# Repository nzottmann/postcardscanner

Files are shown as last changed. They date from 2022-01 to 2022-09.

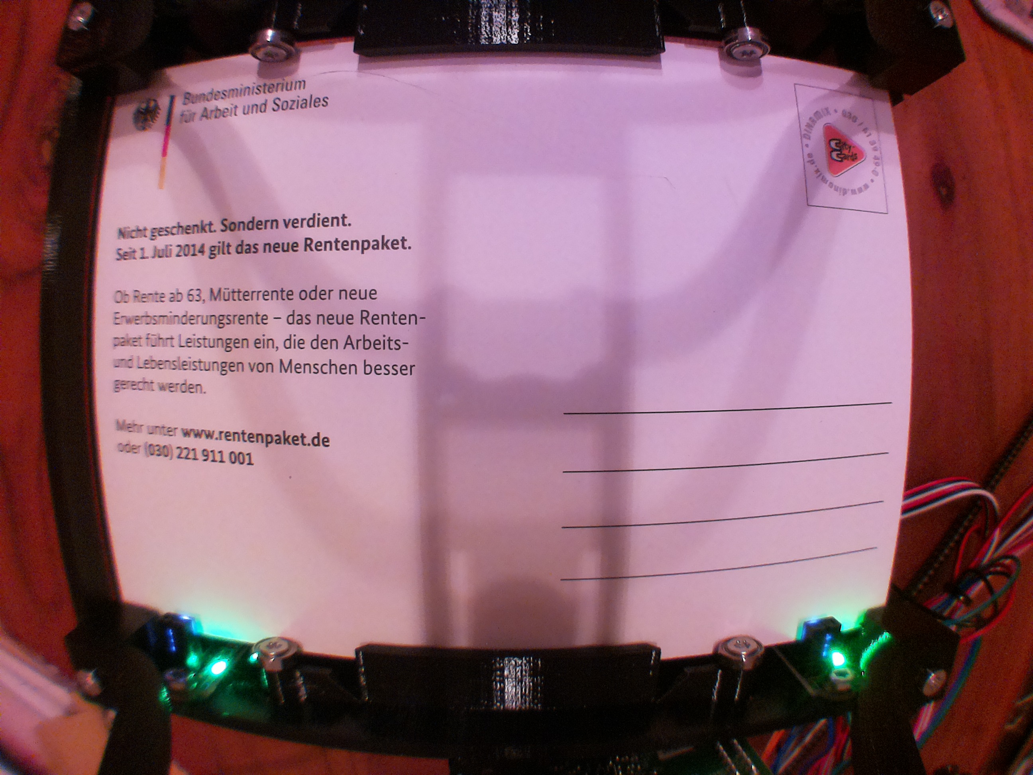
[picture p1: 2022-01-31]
examples/example.jpg

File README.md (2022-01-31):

Python library for postcard scanner

# Installation
Installation manual is for linux, tested on Raspberry Pi (Raspberry Pi OS, bullseye, Release date: January 28th 2022)
- Install Python >=3.5.
- Install python venv
    ```
    sudo apt-get install python3-venv
    ```
- Create and activate virtual environment
    ```
    source venv/bin/activate
    python3 -m venv venv
    ```
- Clone this repo
    ```
    git clone https://github.com/nzottmann/postcardscanner.git
    ```
- Install `postcardscanner`
    ```
    pip install -e postcardscanner
    ```
- Run example
    ```
    cd postcardscanner/examples
    python scanner_demo.py
    ```
    Output:
    ```
    DEBUG:postcardscanner:state: enabled
    Received image
    DEBUG:postcardscanner:state: scanning
    DEBUG:postcardscanner:state: enabled
    ```
    `img.jpg` is now a copy of `example.jpg`

# Usage
Examples in `examples` folder show how to use this library.

## Examples

### scanner_v0.py
Example for using the first hardware prototype, v0

### scanner_demo_camera.py
Example for testing without scanner hardware, but with pi camera. Captures images from camera.

### scanner_demo.py
Example for testing without hardware. Input own image for testing or use `example.jpg`.

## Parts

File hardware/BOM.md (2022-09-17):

# Postcardscanner Bill of Materials

## 3D printed Parts

For printing, Prusament PETG and a Prusa printer with a 0.6mm nozzle is recommended. Use supports where necessary.

See 3d construction file for placment of these parts:

- base
- frame-bot (needs supports)
- frame-bot-cover
- frame-top
- 4x sensor cover
- feeder
- belt-cover
- camera
  - camera-mount
  - wall-front
  - wall-back
- 4x roller (use TPU, FilaFlexible40 recommended)

## Mechanical

- Misumi
  - 8x bearings 695DD1 13x5x4mm RS/2RS
  - 1x axis PSFMRR5-140-B2-S18.4
  - 1x axis PSFMRR5-156.4-B18.4-S18.4
  - 4x retainer NETWS4
  - 1x belt GBN2502GT-60 2GT 6mm 250mm
- Amazon
  - 4x Pulley GT2 20 teeth for 5mm shaft, 6mm belt
  - Ruthex M3 brass inserts
- stepperonline
  - Nema 11 Bipolar 1.8deg 7Ncm 28x28x31mm

## Electrical

- Raspberry Pi Camera v2
- Camera flex cable 50cm
- 4x optical endstop
- 12V LED stripe, ~20cm
- Cable

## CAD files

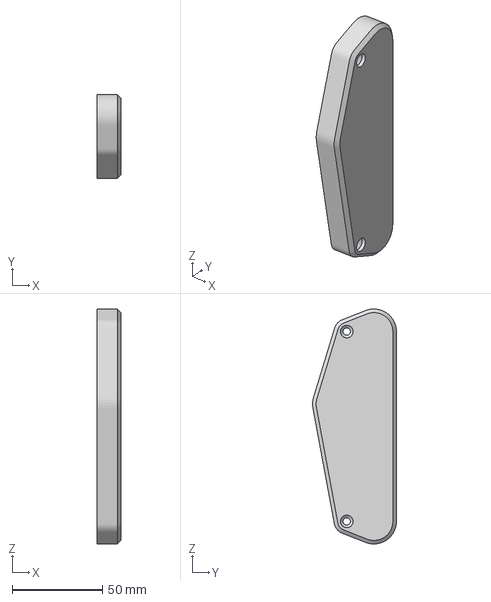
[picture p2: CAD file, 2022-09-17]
hardware/3d printing/belt-cover.3mf
13.2 x 46.4 x 130.0 mm

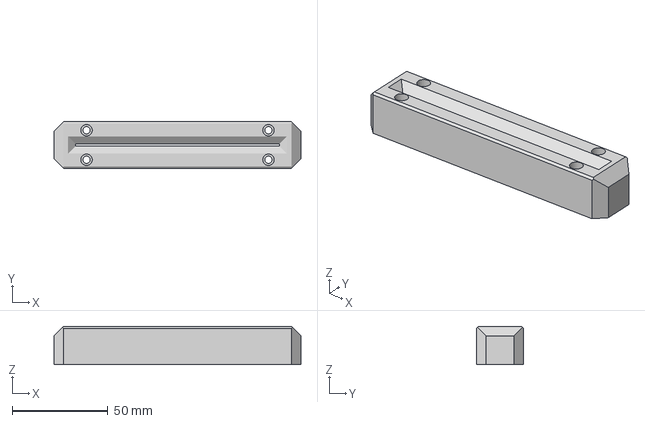
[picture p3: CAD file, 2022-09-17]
hardware/3d printing/feeder.3mf
129.0 x 24.4 x 20.0 mm

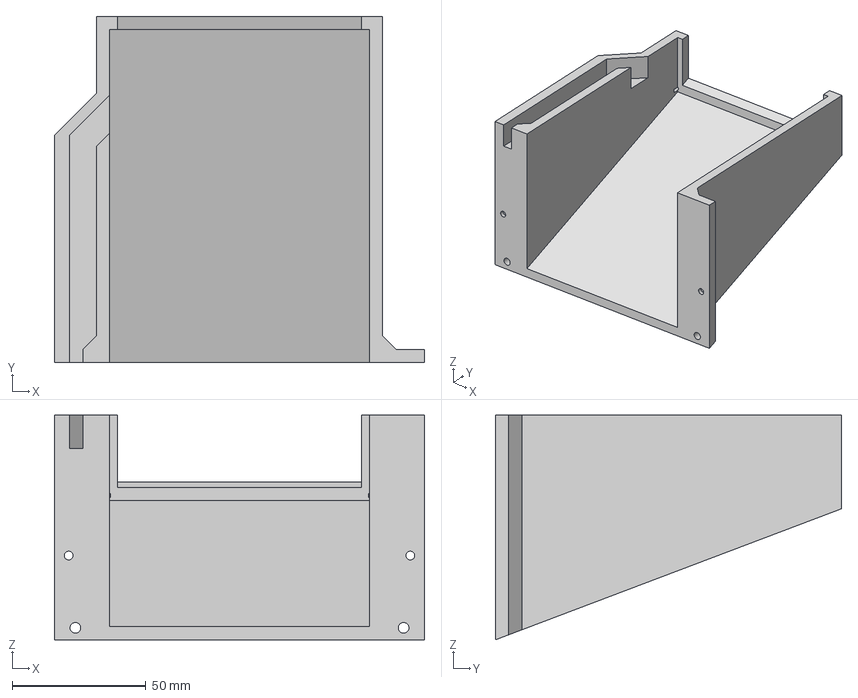
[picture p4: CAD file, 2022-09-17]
hardware/3d printing/wall-back.3mf
138.2 x 129.4 x 84.0 mm

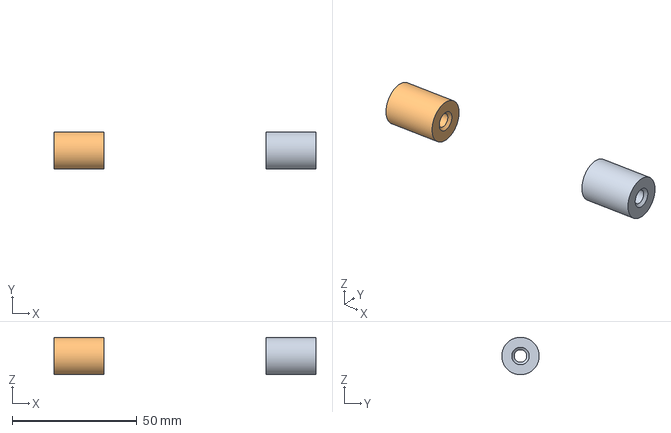
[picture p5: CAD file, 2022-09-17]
hardware/3d printing/roller.3mf
105.0 x 15.0 x 15.0 mm
Körper1
Körper3

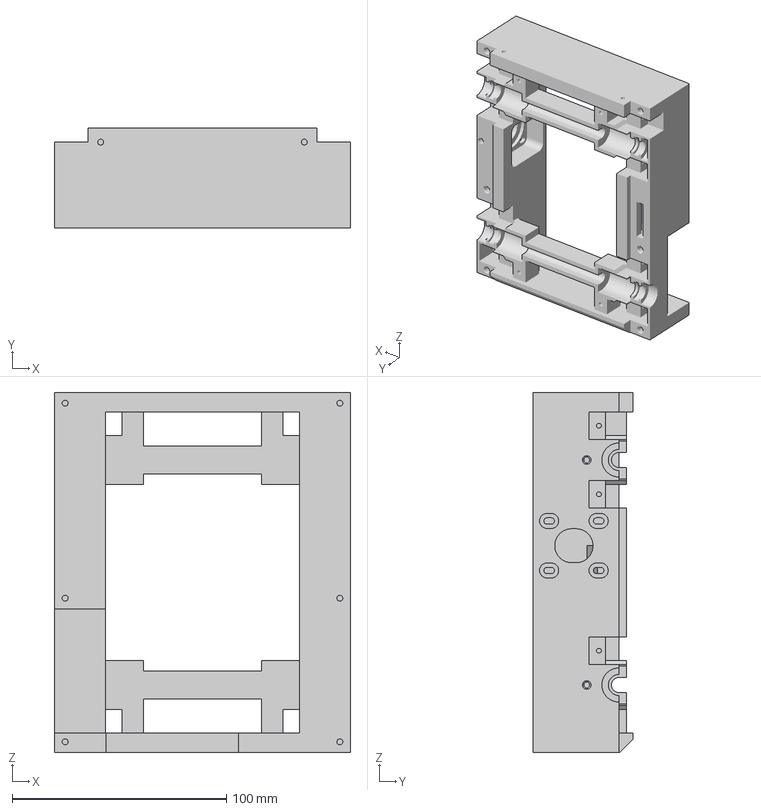
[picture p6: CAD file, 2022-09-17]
hardware/3d printing/frame-bot.3mf
138.2 x 46.5 x 168.0 mm

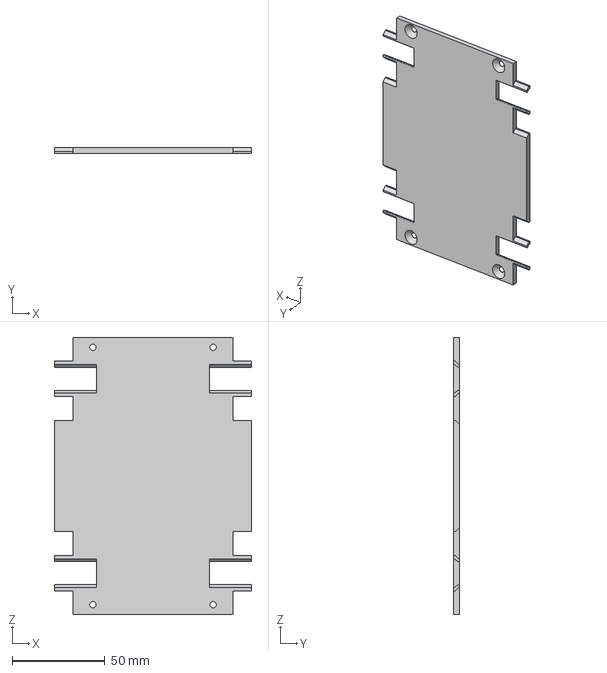
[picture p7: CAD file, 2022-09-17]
hardware/3d printing/frame-bot-cover.3mf
106.6 x 3.00 x 149.6 mm

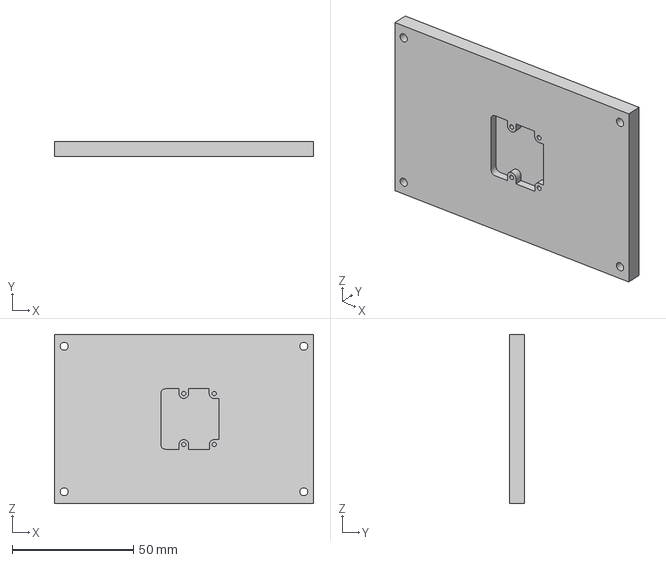
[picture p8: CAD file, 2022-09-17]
hardware/3d printing/camera-mount.3mf
107.0 x 6.00 x 70.0 mm

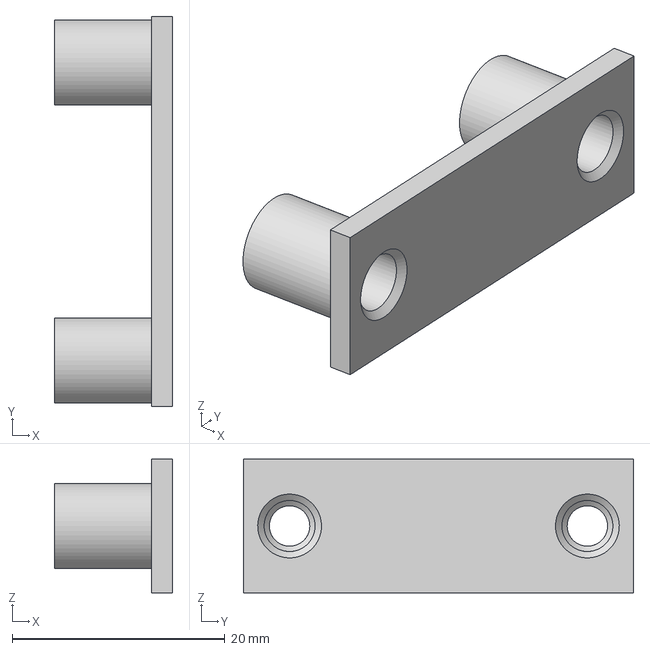
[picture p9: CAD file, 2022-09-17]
hardware/3d printing/sensor-cover.3mf
11.1 x 36.7 x 12.6 mm

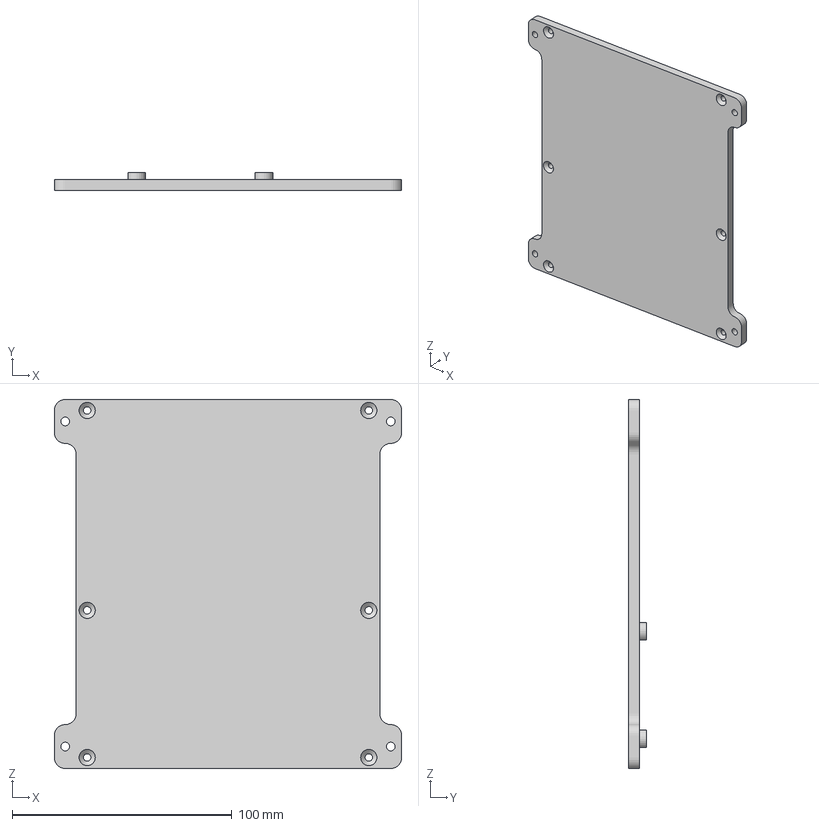
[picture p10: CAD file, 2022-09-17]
hardware/3d printing/base.3mf
158.2 x 8.01 x 168.0 mm

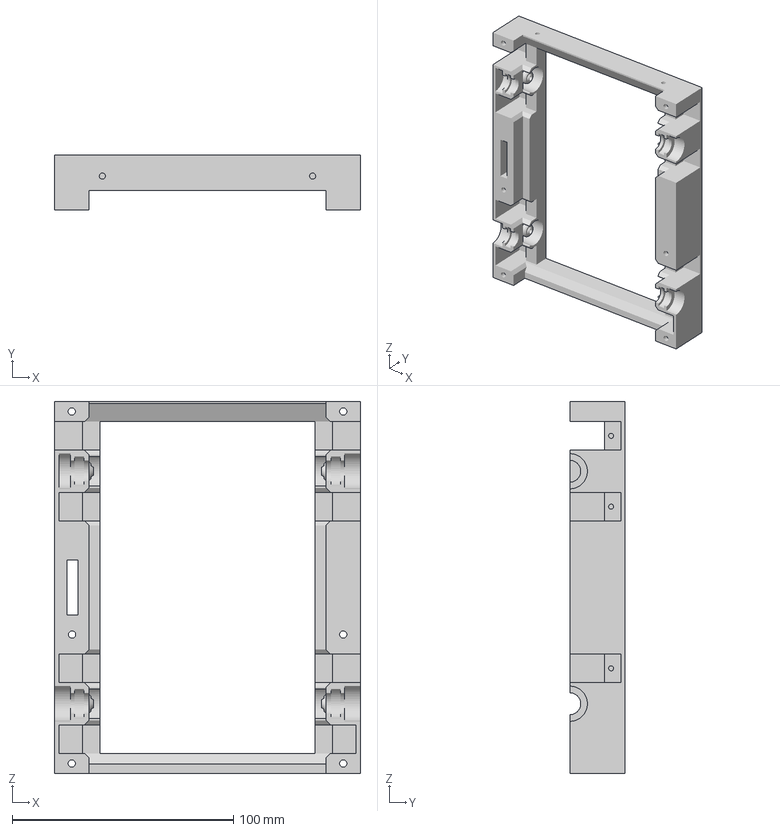
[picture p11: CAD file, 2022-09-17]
hardware/3d printing/frame-top.3mf
138.2 x 25.0 x 168.0 mm

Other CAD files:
hardware/3d printing/wall-front.3mf

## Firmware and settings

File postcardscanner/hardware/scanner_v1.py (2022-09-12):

import logging
logger = logging.getLogger('scanner_v1')
import time
from io import BytesIO
import subprocess
import RPi.GPIO as GPIO
from RpiMotorLib import RpiMotorLib
from .scanner import Scanner
from postcardscanner.states import PostcardScannerState

class ScannerV1(Scanner):
    clockwise = False
    steptype_1 = "Half"
    steptype_2 = "Half"
    stepdelay = .0003
    counter = 0
    def __init__(self, callback, pins={
        'dir': 4,
        'step': 17,
        'mode': (22, 27, 18),
        's1': 16,
        's2': 19,
        's3': 20,
        's4': 21,
        'sleep': 23,
        'led': 12
    }):
        self.pins = pins
        self.callback = callback
        GPIO.setwarnings(False)
        GPIO.setmode(GPIO.BCM)

        # GPIOs
        GPIO.setup((pins['s1'], pins['s2'], pins['s3'], pins['s4']), GPIO.IN)
        GPIO.setup((pins['sleep'], pins['led']), GPIO.OUT)

        self.motor = RpiMotorLib.A4988Nema(pins['dir'], pins['step'], pins['mode'], "DRV8825")
        
        self._init_state()
        
    def _sns(self, sensor):
        sensors = ('s1', 's2', 's3', 's4')
        return GPIO.input(self.pins[sensors[sensor]])
        
    def _mot_sleep(self, state):
        GPIO.output(self.pins['sleep'], state)
        
    def _led(self, state):
        GPIO.output(self.pins['led'], state)
        
    def _init_state(self):
        if not self._sns(0) and not self._sns(1):
            self.pos = 0
        else:
            self.pos = 2
        
    def capture(self):
        process = subprocess.Popen(
            ['libcamera-still', '-n', '-t', '1', '-o', '-'],
            stdout=subprocess.PIPE,
            stderr=subprocess.DEVNULL
        )        
        return BytesIO(process.stdout.read())
    
    def loop(self):
        if self.pos == 0:
            if self._sns(0) and self._sns(1):
                self.pos = 1
                self._mot_sleep(1)
                self.counter = 0
            else:
                self._mot_sleep(0)
                time.sleep(0.1)
                return PostcardScannerState.enabled
        if self.pos == 1:
            self.counter += 1
            if self.counter > 50:
                self.pos = 99
            self.motor.motor_go(self.clockwise, self.steptype_1, 100, self.stepdelay, False, 0)
            if not self._sns(0) or not self._sns(1):
                self.pos = 0
            if self._sns(2):
                self.pos = 2
                self.counter = 0
            else:
                return PostcardScannerState.scanning
        if self.pos == 2:
            self.counter += 1
            if self.counter > 100:
                self.pos = 99
            self.motor.motor_go(self.clockwise, self.steptype_1, 100, self.stepdelay, False, 0)
            if not self._sns(2):
                self.pos = 1
            if self._sns(3):
                self.pos = 3
                self.counter = 0
            return PostcardScannerState.scanning
        if self.pos == 3:
            self.counter += 1
            if self.counter > 100:
                self.pos = 99
            self.motor.motor_go(self.clockwise, self.steptype_1, 100, self.stepdelay, False, 0)
            if not self._sns(1):
                self.motor.motor_go(not self.clockwise, self.steptype_1, 100, self.stepdelay, False, 0)
                self._mot_sleep(0)
                self._led(1)
                try:
                    self.callback(self.capture())
                except Exception as e:
                    logger.error(f'Capture callback raised exception: {e}')
                self._led(0)
                self._mot_sleep(1)
                #time.sleep(1)
                self.pos = 4
                self.counter = 0
            return PostcardScannerState.scanning
        if self.pos == 4:
            self.counter += 1
            if self.counter > 3:
                self.pos = 99
            self.motor.motor_go(self.clockwise, self.steptype_2, 3000, .00005, False, 0)
            if not self._sns(3):
                self.motor.motor_go(self.clockwise, self.steptype_2, 3000, .00005, False, 0)
                self._mot_sleep(0)
                self.pos = 0
            return PostcardScannerState.scanning
        if self.pos == 99:
            self._mot_sleep(0)
            if self._sns(0) or self._sns(1) or self._sns(2) or self._sns(3):
                time.sleep(0.1)
                return PostcardScannerState.error
            else:
                self.pos = 0
        
        return PostcardScannerState.enabled

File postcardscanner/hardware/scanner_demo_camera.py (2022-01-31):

import time
from io import BytesIO
import subprocess
from .scanner import Scanner
from postcardscanner.states import PostcardScannerState

class ScannerDemoCamera(Scanner):
    scanning = False
    def __init__(self, callback):
        self.callback = callback
        
    def capture(self):
        process = subprocess.Popen(
            ['libcamera-still', '-n', '-t', '1', '-o', '-'],
            stdout=subprocess.PIPE,
            stderr=subprocess.DEVNULL
        )        
        return BytesIO(process.stdout.read())
        
    def simulate_scan(self, image=None):
        self.scanning = True
        self.callback(self.capture())
    
    def loop(self):
        time.sleep(1)
        if self.scanning:
            self.scanning = False
            return PostcardScannerState.scanning
        return PostcardScannerState.enabled

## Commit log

2022-01-31 Scan image, refactor thread
2022-09-17 Add BOM and §D printing files
    [base.3mf, belt-cover.3mf, camera-mount.3mf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]
